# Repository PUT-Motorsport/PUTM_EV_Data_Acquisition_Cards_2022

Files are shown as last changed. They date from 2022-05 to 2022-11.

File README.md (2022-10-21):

# PUTM_EV_Data_Acquisition_Card_2022

## About the project
It's main task is to receive signals from sensors mounted on the car and analyze them and send to CAN-bus.

## Hardware design
The hardware part of the project is the PCB board which is connected to the sensors and CAN-bus. The microcontroller which is used is STM32L4P5RET6. The PCB is supply by 5VDC.

## Sensors
It receive signals from :   
 - ~~inductive sensors - there are used to measure wheels rotation speed~~
 - brake pressure sensors - which measure the pressure in the brake system
 - shutdown circuit sense:
1. BSPD
2. Overtravel switch
3. Driver's kill switch
4. Left and right kill switches
 - acceleration - from MPU on board

## Program flow diagram

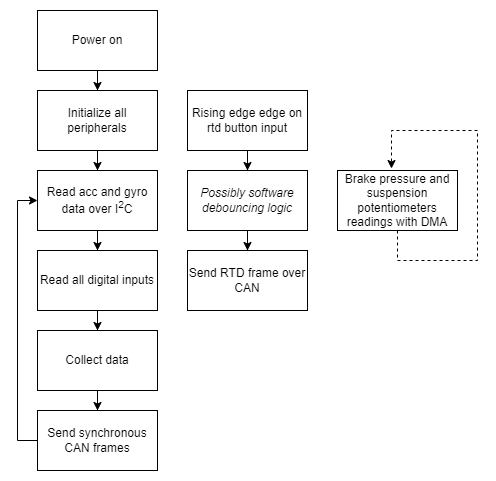
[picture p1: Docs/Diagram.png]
Program flow diagram
)

## DMA and ADC timings consideration

The program is required to collect and relay data @ 100 ms.
Two adc peripherals are used to collect data from 3 analog sensors each.

* * *
ADC clock frequency: $32 MHz$

Sampling time: $92.5$ cycles - **reason:** High impedance inputs are used, subject to change

Oversampling: by 256

Sample conversion time: $T_{sample} + 12.5 = 105 cycles$

With oversampling: $T_{total} = 105 cycles * 256 samples = 26880 cycles$

$$
t = \frac{26800 * 3 channels}{32 * 10^6 Hz} = 2.52 * 10^{-3} s = 2.52 ms
$$

# 1D Kalman filter design for the IMU data

$$
\vec{x}(t + 1) = F(t + 1; t) * \vec{x}(t) + G * \vec{u} + w(t)
$$
$$
\vec{z} = H * \vec{x}(t)
$$

$$
\vec{x} = \begin{bmatrix} a_x \\ a_y \\ a_z \end{bmatrix}
$$

$$
F = \begin{bmatrix} 1 \\ 1 \\ 1 \end{bmatrix} \space\space\space H = \begin{bmatrix} 1 \\ 1 \\ 1 \end{bmatrix} \space\space\space G = [1] \space u = [0]
$$

$$
P(t + 1) = F(t)P(t) F(t)^T + Q(t)
$$

Since there is no way to calculate the change in acceleration, w(t) is estimated to gaussian N(0, $\sigma$) as process noise.

$$
Q(t) = \begin{bmatrix} \sigma_x \space 0 \space 0 \\ 0 \space \sigma_y \space 0 \\ 0 \space 0 \space \sigma_z\end{bmatrix}
$$

$$
\sigma_{process} = \sigma_x = \sigma_y = \sigma_z
$$

$$
R = \begin{bmatrix} ? ? ? \\ ? ? ? \\ ? ? ? \end{bmatrix}
$$

R to be selected.

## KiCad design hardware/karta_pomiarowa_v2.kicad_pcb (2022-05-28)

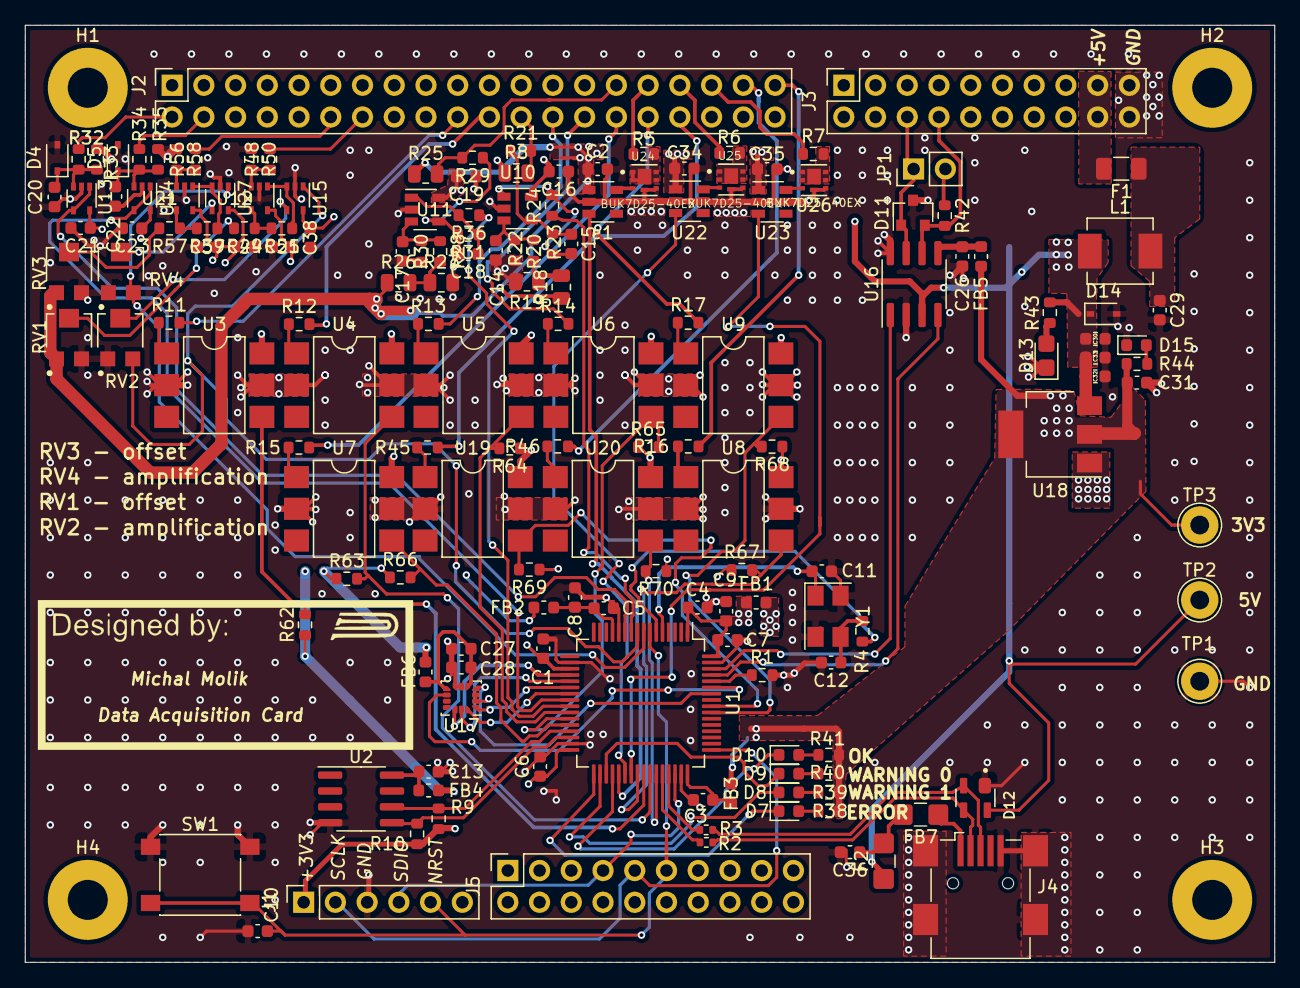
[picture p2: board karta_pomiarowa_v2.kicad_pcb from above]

Board: 4 copper layers, 100.0 x 75.0 mm, 168 parts (0 on the bottom side), 118 nets.

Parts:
C1, C2, C3, C4, C5, C6, C7, C10, C13, C27, C28, C30, C31, C33, C34, C35, C36: 100nF; C_0603_1608Metric
C8: 1uF; C_0603_1608Metric
C9: 4.7uF; C_0603_1608Metric
C11, C12: 20p; C_0603_1608Metric
C14, C15, C17, C18: 1nF; C_0603_1608Metric
C16, C19, C20, C21, C22, C23, C24, C25, C26, C37, C38: 100n; C_0603_1608Metric
C29, C32: 10uF; C_0603_1608Metric
D4, D5: 6v5; D_SOD-323
D7, D8, D9, D10, D15: LED; LED_0603_1608Metric
D11: PESD2CAN.215; SOT-23
D12: PRTR5V0U2X; SOT190P230X110-4N
D13: LED; D_0805_2012Metric_Castellated
D14: 5.6v/6v; D_SOD-323
F1: 200mA; Fuse_1206_3216Metric
F2: 200mA; Fuse_1206_3216Metric_Castellated
FB1, FB2, FB3, FB4, FB5, FB6: 60R120MHz; L_0603_1608Metric
FB7: 1kOhm; Fuse_1206_3216Metric_Castellated
H1, H2, H3, H4: MountingHole; MountingHole_3.2mm_M3_Pad
J1: Conn_01x05_Male; PinSocket_1x06_P2.54mm_Vertical
J2: Conn_02x20_Odd_Even; PinSocket_2x20_P2.54mm_Vertical
J3, J5: Conn_02x10_Odd_Even; PinSocket_2x10_P2.54mm_Vertical
J4: USB_OTG; USB_Mini-B_Wuerth_65100516121_Horizontal
JP1: Jumper_NO_Small; PinHeader_1x02_P2.54mm_Vertical
L1: 6.8uH; L_Vishay_IHLP-2020
R1, R20, R21, R28, R29, R49, R57: 10k; R_0603_1608Metric
R2, R3: 22R; R_0402_1005Metric
R4, R42: R; R_0603_1608Metric
R5, R6, R7: 10R; R_0603_1608Metric
R8, R18, R19, R25, R26, R27: 5k; R_0805_2012Metric
R9, R10: 4.7k; R_0603_1608Metric
R11, R12, R13, R14, R15, R16, R17, R45, R46: 12k; R_0603_1608Metric
R22, R23, R30, R31, R51, R59: 47k; R_0603_1608Metric
R24, R36: 100R; R_0603_1608Metric
R32, R34, R48, R56, R62, R63, R64, R65, R66, R67, R68, R69, R70: 1k; R_0603_1608Metric
R33, R35, R38, R39, R40, R41, R44, R50, R58: 2k; R_0603_1608Metric
R43: 2.5k; R_0603_1608Metric
RV1, RV3: 2K; TRIM_TC33X-2-103E
RV2, RV4: 3K; TRIM_TC33X-2-103E
SW1: SW_MEC_5E; SW_Push_1P1T_NO_6x6mm_H9.5mm
TP1: GND; TestPoint_THTPad_D3.0mm_Drill1.5mm
TP2: 5V; TestPoint_THTPad_D3.0mm_Drill1.5mm
TP3: 3V3; TestPoint_THTPad_D3.0mm_Drill1.5mm
U1: STM32L4P5RET6; LQFP-64_10x10mm_P0.5mm
U2: M24C01-WMN; SOIC-8_3.9x4.9mm_P1.27mm
U3, U4, U5, U6, U7, U8, U9, U19, U20: H11L1; SMDIP-6_W7.62mm
U10, U11: TSX7191; SOT-23-5
U12, U13, U14, U15, U21, U27: MCP6001x-LT; SOT-353_SC-70-5
U16: ATA6561-GAQW-N; SOIC-8_3.9x4.9mm_P1.27mm
U17: IMS330DHCX; LGA-14_3x2.5mm_P0.5mm_LayoutBorder3x4y
U18: LM1117-3.3_copy; SOT-223
U22, U23: MCP14A0052T; SOT-23-6
U24, U25, U26: BUK7D25-40EX; TRANS_PMPB16EPX
Y1: 8MHz; Crystal_SMD_5032-4Pin_5.0x3.2mm
e1: MCP14A0052T; SOT-23-6

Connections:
+3V3: C16.2, C19.2, C21.2, C23.2, C24.2, C25.2, C31.1, C37.2, C38.2, FB1.1, FB2.1, FB3.1, FB4.1, FB5.1, FB6.1, J1.1, R9.1, R10.1, R38.1, R39.1, R40.1, R41.1, R44.1, R62.1, R63.1, R64.1, R65.1, R66.1, R67.1, R68.1, R69.1, R70.1, TP3.1, U3.6, U4.6, U5.6, U6.6, U7.6, U8.6, U9.6, U10.5, U11.5, U12.5, U13.5, U14.5, U15.5, U18.2, U18.4, U19.6, U20.6, U21.5, U27.5
+5V: C2.2, C30.1, C32.1, C33.1, C34.2, C35.2, D12.4, D14.1, F2.1, L1.1, R8.1, R18.1, R25.1, R26.1, R43.1, RV1.1, RV3.1, TP2.1, U16.3, U18.3, U22.1, U23.1, e1.1
+5VP: F1.2, J3.17, J3.18
/+uC: C1.1, C4.1, C6.1, C7.1, C9.1, FB1.2, U1.1, U1.19, U1.32, U1.64
/+uCa: C5.1, C8.1, FB2.2, U1.13
/+uCusb: C3.1, FB3.2, U1.48
/A0: RV4.3, U1.8, U27.1
/A1: RV2.3, U1.9, U15.1
/A2: R24.1, U1.10
/A3: U1.11, U13.1, U13.4
/A4: U1.24, U14.1, U14.4
/A5: R36.1, U1.25
/CAN_RX: U1.61, U16.4
/CAN_TRASCIVER/+3.3V_CAN: C26.1, FB5.2, U16.5
/CAN_TX: U1.62, U16.1
/DI0: R64.2, U1.26, U5.4
/DI1: R65.2, U1.27, U6.4
/DI2: R66.2, U1.28, U7.4
/DI3: R68.2, U1.55, U9.4
/DI4: R69.2, U1.56, U19.4
/DO0: U1.37, e1.3
/DO1: U1.38, U22.3
/DO2: U1.39, U23.3
/EEPROM/+3.3V_ee: C13.1, FB4.2, U2.8
/EEPROM_SCL: R9.2, U1.29, U2.6
/EEPROM_SDA: R10.2, U1.30, U2.5
/ISM330DHCXTR/+3.3V_IMS: C27.1, C28.1, FB6.2, U17.5, U17.8
/ISM_INT1: U1.58, U17.4
/ISM_INT2: U1.59, U17.9
/LED0: D7.1, U1.33
/LED1: D8.1, U1.34
/LED2: D9.1, U1.35
/LED3: D10.1, U1.36
/Left_s/IN+: R26.2, R27.1, R28.2
/OSC_IN: C11.2, U1.5, Y1.1
/OSC_OUT: R4.1, U1.6
/Right_s/IN+: R18.2, R19.1, R20.2
/SPI_CLK: U1.21, U17.13
/SPI_CS: U1.20, U17.12
/SPI_MISO: U1.22, U17.1
/SPI_MOSI: U1.23, U17.14
/TIM1_CH3: R70.2, U1.43, U20.4
/TIM3_CH4: R67.2, U1.40, U8.4
/WSS_TIM1_CH1: R62.2, U1.41, U3.4
/WSS_TIM1_CH2: R63.2, U1.42, U4.4
BRK_PRESS1: J2.12, R56.2
BRK_PRESS2: J2.14, R48.2
CANH: D11.1, J3.6, JP1.1, U16.7
CANL: D11.2, J3.8, R42.2, U16.6
GND: C1.2, C2.1, C3.2, C4.2, C5.2, C6.2, C7.2, C8.2, C9.2, C10.2, C11.1, C12.2, C13.2, C14.2, C16.1, C17.2, C19.1, C20.2, C21.1, C22.2, C23.1, C24.1, C25.1, C26.2, C27.2, C28.2, C29.2, C30.2, C31.2, C32.2, C33.2, C34.1, C35.1, C36.2, C37.1, C38.1, D4.2, D5.2, D11.3, D12.1, D13.1, D14.2, D15.1, J1.3, J3.19, J3.20, J4.5, J4.6, R1.2, R19.2, R22.2, R27.2, R30.2, R33.1, R35.1, R50.1, R58.1, RV1.3, RV2.1, RV3.3, RV4.1, SW1.1, TP1.1, U1.12, U1.18, U1.31, U1.47, U1.63, U2.4, U3.2, U3.5, U4.2, U4.5, U5.2, U5.5, U6.2, U6.5, U7.2, U7.5, U8.2, U8.5, U9.2, U9.5, U10.2, U11.2, U12.2, U13.2, U14.2, U15.2, U16.2, U16.8, U17.2, U17.3, U17.6, U17.7, U18.1, U19.2, U19.5, U20.2, U20.5, U21.2, U22.2, U22.5, U23.2, U23.5, U24.4, U24.8, U25.4, U25.8, U26.4, U26.8, U27.2, Y1.2, Y1.4, e1.2, e1.5
INERTIA: J2.32, R17.2
KILL_DRIVER: J2.26, R13.2
KILL_LEFT: J2.30, R15.2
KILL_RIGHT: J2.28, R14.2
NRST: C10.1, J1.5, J5.11, SW1.2, U1.7
unnamed: C12.1, R4.2, Y1.3
unnamed: C14.1, R20.1, R22.1, U10.3
unnamed: C15.1, R23.1, R24.2, U10.1
unnamed: C15.2, R21.1, R23.2, U10.4
unnamed: C17.1, R28.1, R30.1, U11.3
unnamed: C18.1, R31.1, R36.2, U11.1
unnamed: C18.2, R29.1, R31.2, U11.4
unnamed: C20.1, D4.1, R32.1, R33.2, U13.3
unnamed: C22.1, D5.1, R34.1, R35.2, U14.3
unnamed: C29.1, F1.1, L1.2
unnamed: C36.1, F2.2, FB7.2
unnamed: D7.2, R38.2
unnamed: D8.2, R39.2
unnamed: D9.2, R40.2
unnamed: D10.2, R41.2
unnamed: D13.2, R43.2
unnamed: D15.2, R44.2
unnamed: FB7.1, J4.1
unnamed: JP1.2, R42.1
unnamed: R1.1, U1.60
unnamed: R2.2, U1.44
unnamed: R3.2, U1.45
unnamed: R5.2, U24.1, U24.2, U24.5, U24.6, U24.7
unnamed: R6.2, U25.1, U25.2, U25.5, U25.6, U25.7
unnamed: R7.2, U26.1, U26.2, U26.5, U26.6, U26.7
unnamed: R11.1, U3.1
unnamed: R12.1, U4.1
unnamed: R13.1, U5.1
unnamed: R14.1, U6.1
unnamed: R15.1, U7.1
unnamed: R16.1, U8.1
unnamed: R17.1, U9.1
unnamed: R45.1, U19.1
unnamed: R46.1, U20.1
unnamed: R48.1, R50.2, U12.3
unnamed: R49.1, R51.2, U12.4
unnamed: R49.2, RV1.2
unnamed: R51.1, U12.1, U15.3
unnamed: R56.1, R58.2, U21.3
unnamed: R57.1, R59.2, U21.4
unnamed: R57.2, RV3.2
unnamed: R59.1, U21.1, U27.3
unnamed: RV2.2, U15.4
unnamed: RV4.2, U27.4
unnamed: U22.6, U25.3
unnamed: U23.6, U26.3
unnamed: U24.3, e1.6
OUTPUT0: J2.31, R5.1
OUTPUT1: J2.33, R6.1
OUTPUT2: J2.35, R7.1
OVERTRAVEL: J2.34, R45.2
PITOT1: J2.2, R32.2
PITOT2: J2.4, R34.2
SCLK: J1.2, J5.9, U1.49
SDIO: J1.4, J5.7, U1.46
SUSP_L: J2.29, R25.2, R29.2
SUSP_R: J2.24, R8.2, R21.2
TIM_IN0: J2.37, R46.2
TIM_IN1: J2.39, R16.2
USB+: D12.2, J4.3, R3.1
USB-: D12.3, J4.2, R2.1
WHSP1: J2.20, R11.2
WHSP2: J2.22, R12.2

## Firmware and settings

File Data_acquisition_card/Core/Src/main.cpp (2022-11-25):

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
/* Includes ------------------------------------------------------------------*/
#include "main.h"
#include "usb_device.h"

/* USER CODE BEGIN Includes */
#include <cstdint>
#include <numeric>	//limits
#include "common_defs.hpp"
#include "can_functions.hpp"
#include "debugIO.hpp"
#include "main.h"
#include "imu_sensor.hpp"
#include "imu_sensor_compatibility_layer.h"	//function prototypes required by the imu
#include "usb_communication.hpp"
/* USER CODE END Includes */

ADC_HandleTypeDef hadc1;
ADC_HandleTypeDef hadc2;
DMA_HandleTypeDef hdma_adc1;
DMA_HandleTypeDef hdma_adc2;

CAN_HandleTypeDef hcan1;

SPI_HandleTypeDef hspi1;

/* USER CODE BEGIN PV */
volatile uint16_t adc1_buffer[ADC_BUFFER_SIZE]{};
volatile uint16_t adc2_buffer[ADC_BUFFER_SIZE]{};

bool send_rtd_signal_flag;
/* USER CODE END PV */

extern "C" void SystemClock_Config(void);
void PeriphCommonClock_Config(void);
static void MX_GPIO_Init(void);
static void MX_DMA_Init(void);
static void MX_SPI1_Init(void);
static void MX_ADC1_Init(void);
static void MX_ADC2_Init(void);
static void MX_CAN1_Init(void);
/**
  * @brief  The application entry point.
  * @retval int
  */
int main(void)
{
  /* MCU Configuration--------------------------------------------------------*/

  /* Reset of all peripherals, Initializes the Flash interface and the Systick. */
  HAL_Init();

  /* Configure the system clock */
  SystemClock_Config();

/* Configure the peripherals common clocks */
  PeriphCommonClock_Config();

  /* Initialize all configured peripherals */
  MX_GPIO_Init();
  MX_DMA_Init();
  MX_SPI1_Init();
  MX_ADC1_Init();
  MX_ADC2_Init();
  MX_CAN1_Init();
  MX_USB_DEVICE_Init();
  /* USER CODE BEGIN 2 */

  HAL_ADCEx_Calibration_Start(&hadc1, ADC_SINGLE_ENDED);
  HAL_ADCEx_Calibration_Start(&hadc2, ADC_SINGLE_ENDED);

  HAL_ADC_Start_DMA(&hadc1, (uint32_t *) adc1_buffer, ADC_BUFFER_SIZE);	//cast to wider type
  HAL_ADC_Start_DMA(&hadc2, (uint32_t *) adc2_buffer, ADC_BUFFER_SIZE);

  Canbus::initialize(&hcan1);

  //Initialize the IMU
  stmdev_ctx_t sensor_instance;

  sensor_instance.write_reg = &spi_write;
  sensor_instance.read_reg = &spi_read;
  sensor_instance.mdelay = &HAL_Delay;
  sensor_instance.handle = nullptr;	//handle is optional and won't be used

  HAL_Delay(3000);	//in case of a loss of power, the IMU needs ~3 s to be able to connect properly

  IMU::initialize(&sensor_instance);

  /* USER CODE END 2 */

  /* Infinite loop */
  /* USER CODE BEGIN WHILE */
  Device::setState(State::OK);
  uint32_t lastFramesSentTime{};
  while (1)
  {
	  IMU::updateSensorData();	//always poll the sensor when not busy

	  USB_DebugData::set_potentiometers(adc1_buffer[2], adc2_buffer[2]);

	  USB_DebugData::send();

	  if (send_rtd_signal_flag) {
		  Canbus::send_rtd_frame();
		  send_rtd_signal_flag = false;
	  }

	  if (lastFramesSentTime + FRAME_TO_FRAME_TIME < HAL_GetTick()) {

		  Canbus::send_main_frame(reinterpret_cast<volatile ADC1_Data *>(adc1_buffer), reinterpret_cast<volatile ADC2_Data *>(adc2_buffer)); //todo: is it strict aliasing rule violation?
		  auto [acc_x, acc_y, acc_z] = IMU::get_acc_data();
		  auto [gyro_x, gyro_y, gyro_z] = IMU::get_gyro_data();
		  Canbus::send_acc_frame(acc_x, acc_y, acc_z);
		  Canbus::send_gyroscope_frame(gyro_x, gyro_y, gyro_z);
		  lastFramesSentTime = HAL_GetTick();
	  }
    /* USER CODE END WHILE */

    /* USER CODE BEGIN 3 */
  }
  /* USER CODE END 3 */
}

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


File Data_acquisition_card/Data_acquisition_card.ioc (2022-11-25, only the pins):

Mcu.UserName=STM32L4P5RETx
PA10.GPIO_Label=RTD_input
PA10.Signal=GPXTI10
PA11.Signal=USB_OTG_FS_DM
PA12.Signal=USB_OTG_FS_DP
PA4.GPIO_Label=SPI1_CS
PA4.Signal=GPIO_Output
PA5.Signal=SPI1_SCK
PA6.Signal=SPI1_MISO
PA7.Signal=SPI1_MOSI
PB0.GPIO_Label=Kill_driver_sense
PB0.Signal=GPIO_Input
PB1.GPIO_Label=Kill_right_sense
PB1.Signal=GPIO_Input
PB12.GPIO_Label=LED0
PB12.Signal=GPIO_Output
PB13.GPIO_Label=LED1
PB13.Signal=GPIO_Output
PB14.GPIO_Label=LED2
PB14.Signal=GPIO_Output
PB15.GPIO_Label=LED3
PB15.Signal=GPIO_Output
PB2.GPIO_Label=Kill_left_sense
PB2.Signal=GPIO_Input
PB8.Signal=CAN1_RX
PB9.Signal=CAN1_TX
PC0.GPIO_Label=ADC1_BRAKE_PRESSURE_1
PC0.Signal=ADCx_IN1
PC1.GPIO_Label=ADC1_BRAKE_PRESSURE_2
PC1.Signal=ADCx_IN2
PC2.GPIO_Label=ADC1_SUSP_R
PC2.Signal=ADCx_IN3
PC3.GPIO_Label=ADC2_ANALOG_1
PC3.Signal=ADCx_IN4
PC4.GPIO_Label=ADC2_ANALOG_2
PC4.Signal=ADCx_IN13
PC5.GPIO_Label=ADC2_SUSP_L
PC5.Signal=ADCx_IN14

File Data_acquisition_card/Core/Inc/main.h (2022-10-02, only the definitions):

#define ADC1_BRAKE_PRESSURE_1_Pin GPIO_PIN_0
#define ADC1_BRAKE_PRESSURE_1_GPIO_Port GPIOC
#define ADC1_BRAKE_PRESSURE_2_Pin GPIO_PIN_1
#define ADC1_BRAKE_PRESSURE_2_GPIO_Port GPIOC
#define ADC1_SUSP_R_Pin GPIO_PIN_2
#define ADC1_SUSP_R_GPIO_Port GPIOC
#define ADC2_ANALOG_1_Pin GPIO_PIN_3
#define ADC2_ANALOG_1_GPIO_Port GPIOC
#define SPI1_CS_Pin GPIO_PIN_4
#define SPI1_CS_GPIO_Port GPIOA
#define ADC2_ANALOG_2_Pin GPIO_PIN_4
#define ADC2_ANALOG_2_GPIO_Port GPIOC
#define ADC2_SUSP_L_Pin GPIO_PIN_5
#define ADC2_SUSP_L_GPIO_Port GPIOC
#define Kill_driver_sense_Pin GPIO_PIN_0
#define Kill_driver_sense_GPIO_Port GPIOB
#define Kill_right_sense_Pin GPIO_PIN_1
#define Kill_right_sense_GPIO_Port GPIOB
#define Kill_left_sense_Pin GPIO_PIN_2
#define Kill_left_sense_GPIO_Port GPIOB
#define LED0_Pin GPIO_PIN_12
#define LED0_GPIO_Port GPIOB
#define LED1_Pin GPIO_PIN_13
#define LED1_GPIO_Port GPIOB
#define LED2_Pin GPIO_PIN_14
#define LED2_GPIO_Port GPIOB
#define LED3_Pin GPIO_PIN_15
#define LED3_GPIO_Port GPIOB
#define RTD_input_Pin GPIO_PIN_10
#define RTD_input_GPIO_Port GPIOA
#define RTD_input_EXTI_IRQn EXTI15_10_IRQn
#define BSPD_Sense_Pin GPIO_PIN_3
#define BSPD_Sense_GPIO_Port GPIOB
#define Overtravel_sense_Pin GPIO_PIN_4
#define Overtravel_sense_GPIO_Port GPIOB

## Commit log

2022-06-03 eeprom i2c work
2022-10-02 New software (#2)
    * Cleanup
    * Created IOC, wrote some code
    * Re-added the CAN library
    * Wrote CAN routines
    * Wrote RTD and IMU code, minor fixes
    * Minor fixed, verified code with CppCheck
    * Fixed .gitignore, eliminated edgecases, fixed minor mistakes
    * Added IMU as a submodule
    * New IMU logic - works
    * Minor fixes
    * Added logic of averaging IMU readings
    [Data_acquisition_card.ioc, can_functions.cpp]
2022-10-21 Kalman (#3)
    * Implemented and tested the Kalman filter
    * Debugged the Kalman filter; fixed DMA issue
    [Data_acquisition_card.ioc, can_functions.cpp]
2022-11-25 Virtual com port (#4)
    * Added USB VCP communication
    * Added logging via the VCP
    * Fixes
    * Added brake pressure normalization
    * Updated suspension potentiometers simulation
    * Updated the schematic
    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
    [Analog.kicad_sch, Analog.sch, Brake pressure.kicad_sch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]

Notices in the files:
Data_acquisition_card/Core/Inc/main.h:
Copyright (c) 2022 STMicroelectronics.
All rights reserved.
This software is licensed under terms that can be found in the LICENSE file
